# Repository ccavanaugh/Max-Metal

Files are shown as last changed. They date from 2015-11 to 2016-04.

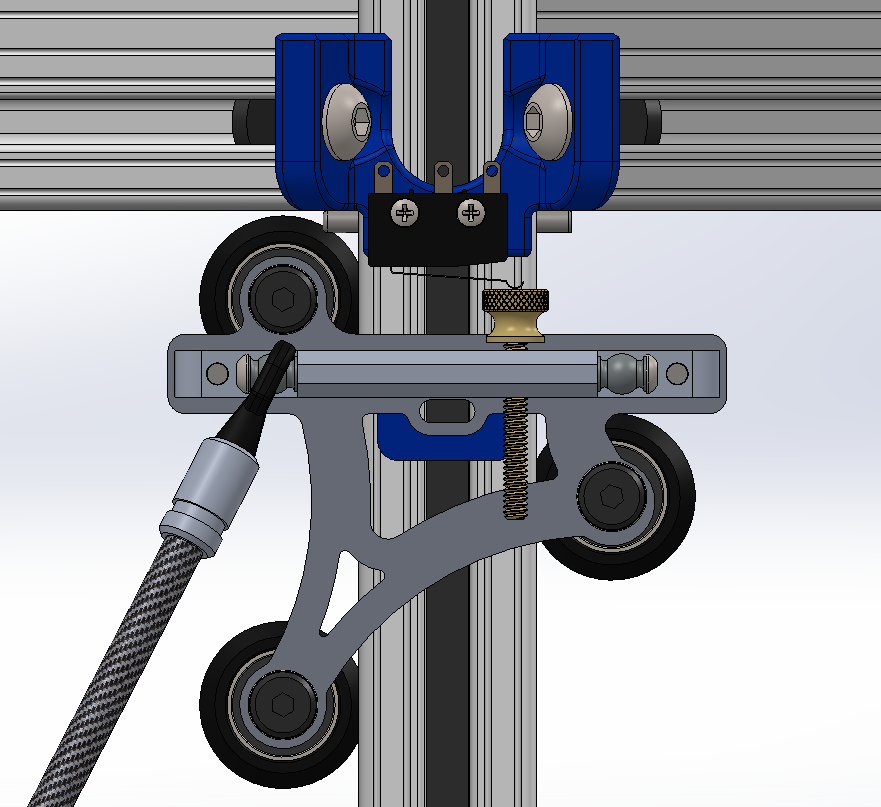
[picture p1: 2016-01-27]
Limit Switch Bracket v2.png

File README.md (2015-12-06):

# Max Metal Delta Printer Files

License
<br />This work is licensed under a <a rel="license" href="http://creativecommons.org/licenses/by-sa/4.0/">Creative Commons Attribution-ShareAlike 4.0 International License</a>.

These files are designed to be used with the all Aluminum Delta printer frame that can be purchased from [Trick Laser](http://www.tricklaser.com/)

## Print recommendations
All parts are deigned to be printed with a layer height of 0.1 mm.  Use of a slicer that can combine infill layers is highly recommended to reduce print time.  
I am printing 0.1 mm layers with 3 stacked layer (0.3 mm) for all sparse infill.  

Slic3r and Kisslicer Pro are known to be capable.  
 
## Small parts
The *Idler Hub* is an optional design vs. using the Open Builds idler assembly.  2 are required for each tower along 
with 2X 11 mm OD X 4 mm Wide x 5 mm ID bearings.  v2 of the part is ment for the thicker idler arms that are now provided
with all kits.

The *Trick Truck Belt Spacer* is required to keep the belt parallel to the axis of travel if you are using Trick Trucks.

These parts must be printed at 100% infill at 0.1 mm layer height. A larger layer height may create dimensional issues
  depending on the slicer used.  
  
  They must be flat!  PLA should provide sufficient strength.
  
## Tensioner Cap
Print at 80-100% infill.  The jack screws will put stress on the parts as will final tightening the of 5mm idler screw.
If you use these, you will need to replace the stock 30mm long idler screw with a 35mm long screw.  A pair of 3mm x 16mm long screws
and 3mm nyloc nuts will be need for tensioning.

## EZStruder Mount
This part is chunky.  We don't want it flexing under heavy retractions and it will see some radiated heat because of
proximity to the stepper motor.  Print with 20% infill.  

ABS or a nylon material is best, but PLA should be fine if your
stepper is not running hot or is actively cooled.

## Power Supply Bracket
Print with 25% or denser infill.  It should not see much heat so PLA is fine.

## Spool Cone
Print with support enabled

## End Stop Cap
Small caps for the end stop screws you can put a wrench on or turn by hand.  Stick the screw through with the head going into the counter-bore.
Fill flush with epoxy.

## Remaining parts
The other parts may be printed with infill and layer heights to suit.

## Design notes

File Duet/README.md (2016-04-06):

Two 0.50" Spacers are needed to support the Duet PCB at one end.  The LED/Connector end will slot and float into the side plate
Max length for the PCB mount screws is 30mm, otherwise it will hit the aluminum extrusion.  You do not want to ground out against the aluminum extrusion.

Use 6-32 X 1" Screws and nylocs to join the plates

Two 6-32 X 1 1/2" Screws and nylocs are used for the LCD housing

The FSR bracket uses 2 3mm x 12mm screws or you can use glue or PSA to attach it to the rear plate.  The FSR board should snap in place, but a small thru hole has been added for a self tapping screw if needed.

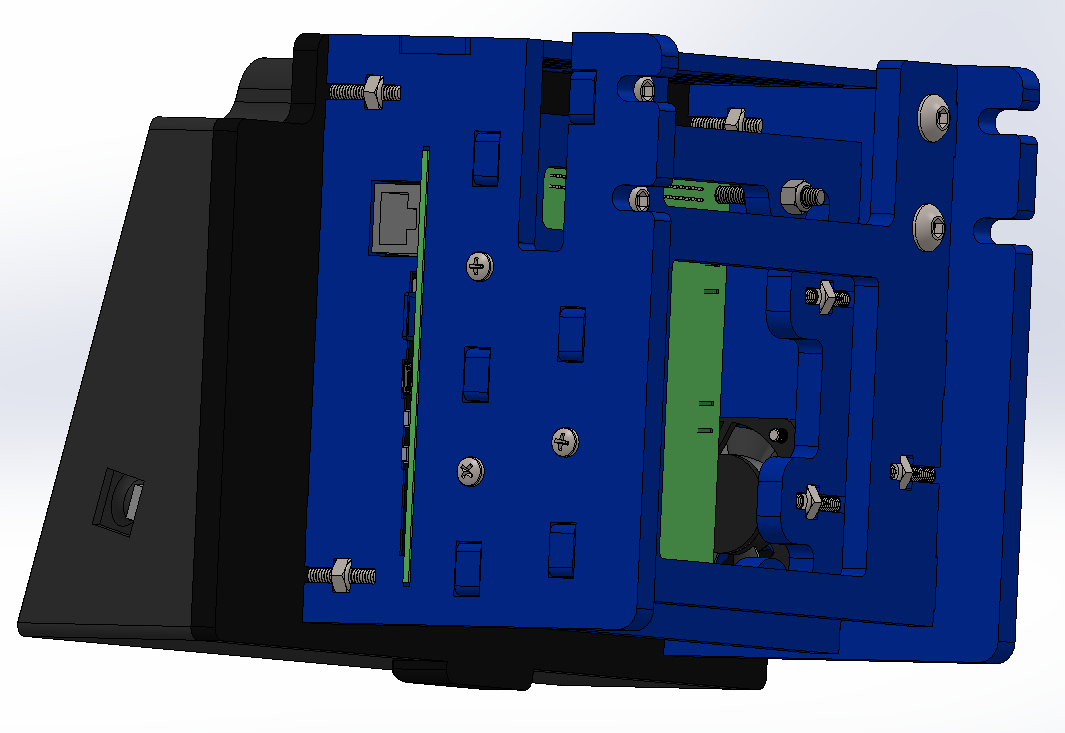
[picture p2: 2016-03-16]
Duet/Side.PNG

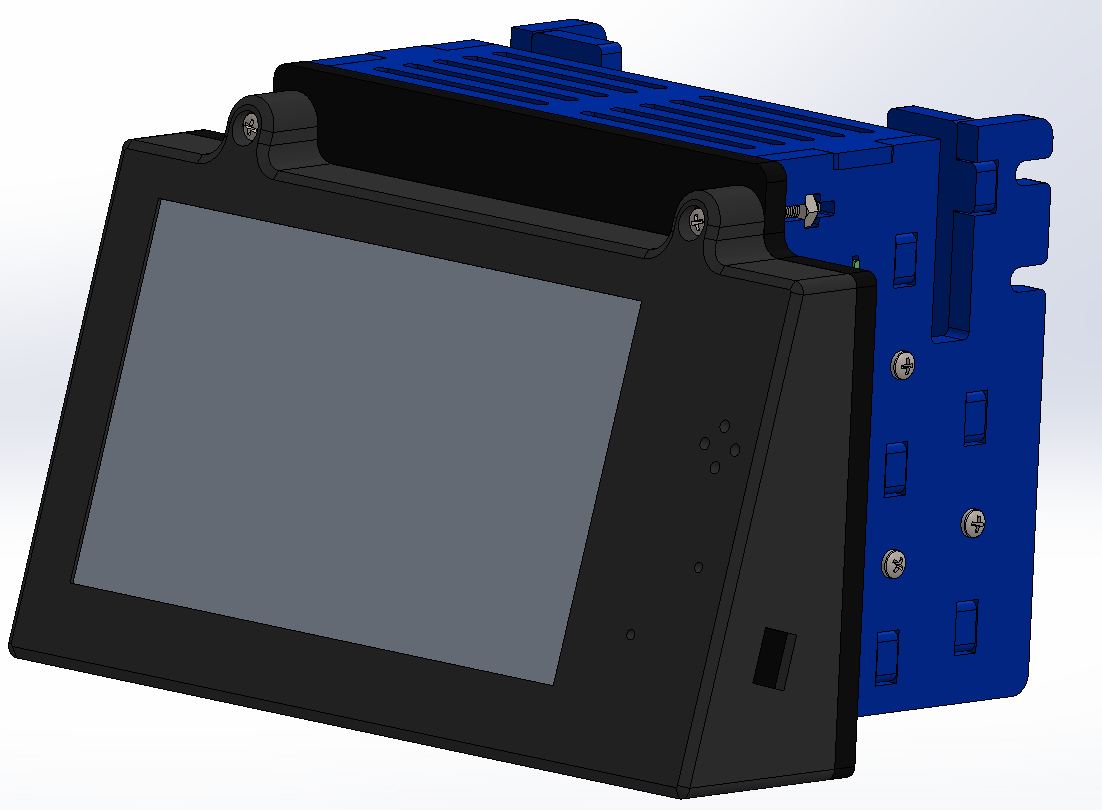
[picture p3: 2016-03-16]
Duet/Front.PNG

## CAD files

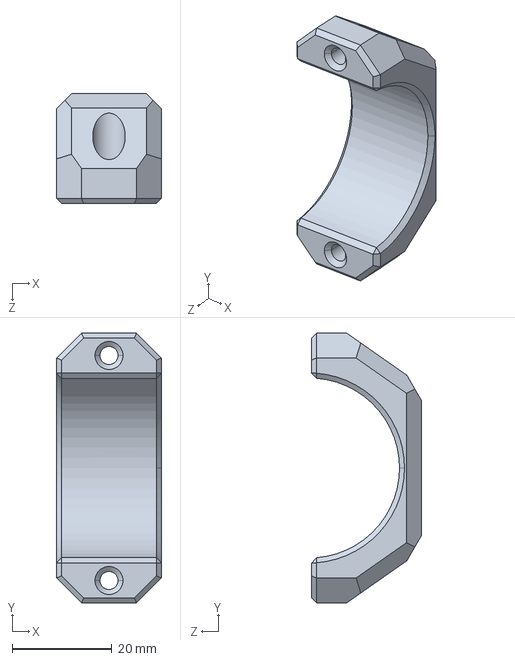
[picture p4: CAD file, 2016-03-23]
BondTech/BondTech Clamp.STEP
21.0 x 54.0 x 22.0 mm

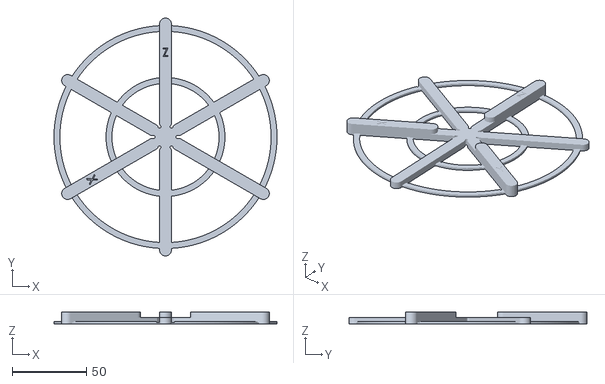
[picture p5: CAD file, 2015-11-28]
Calibration/60 DEGREE CALIBRATION OBJECT.STL
150.0 x 160.0 x 8.20

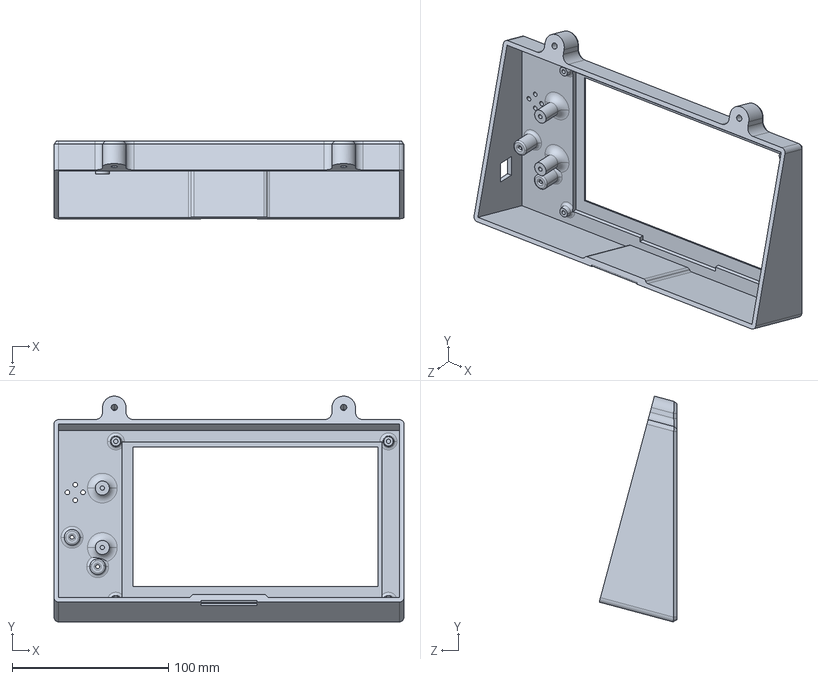
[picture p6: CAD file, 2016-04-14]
Duet/PanelDue 7-LCD Case.STEP
224.0 x 144.5 x 49.6 mm

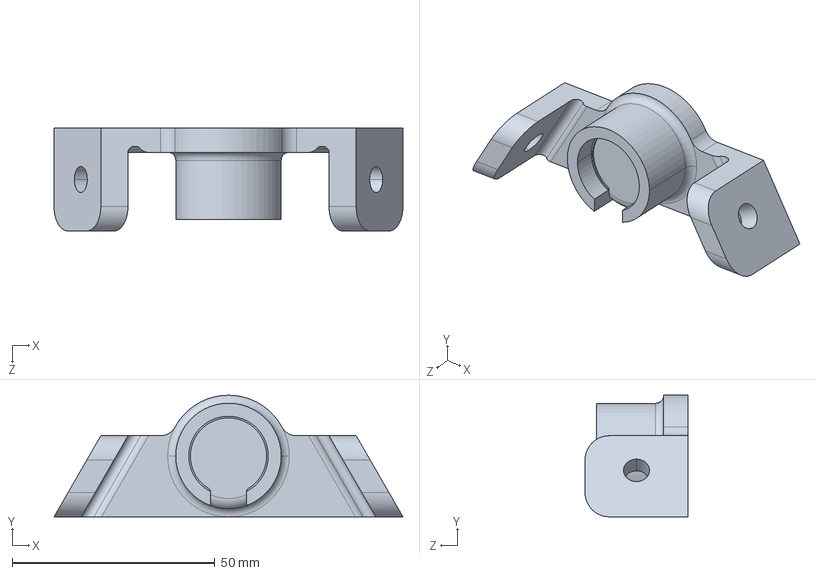
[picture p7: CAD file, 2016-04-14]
FSR BRACKET-Z.STEP
86.1 x 30.0 x 25.4 mm

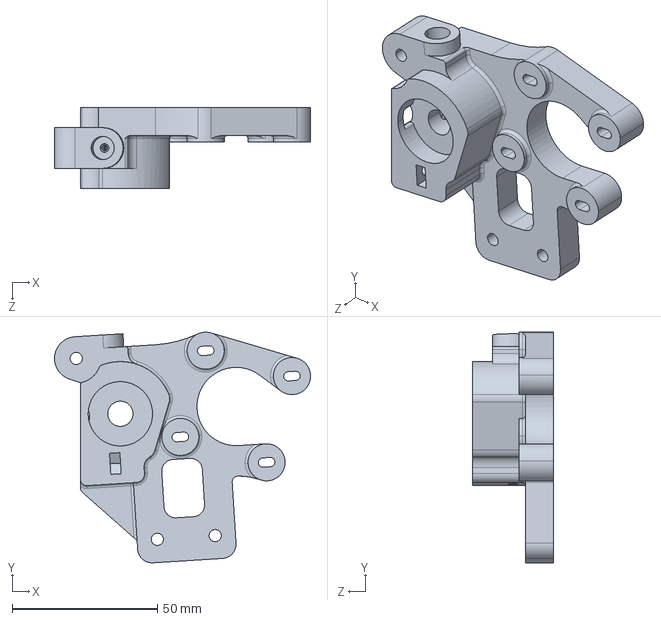
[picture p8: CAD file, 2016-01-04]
Geared Extuder/Extruder Frame - Delta.STEP
88.3 x 79.5 x 28.0 mm

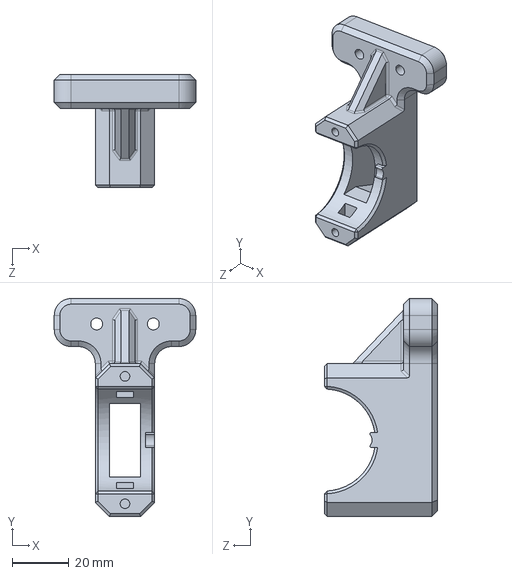
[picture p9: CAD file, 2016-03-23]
BondTech/BondTechBracket.STEP
50.0 x 77.0 x 40.0 mm

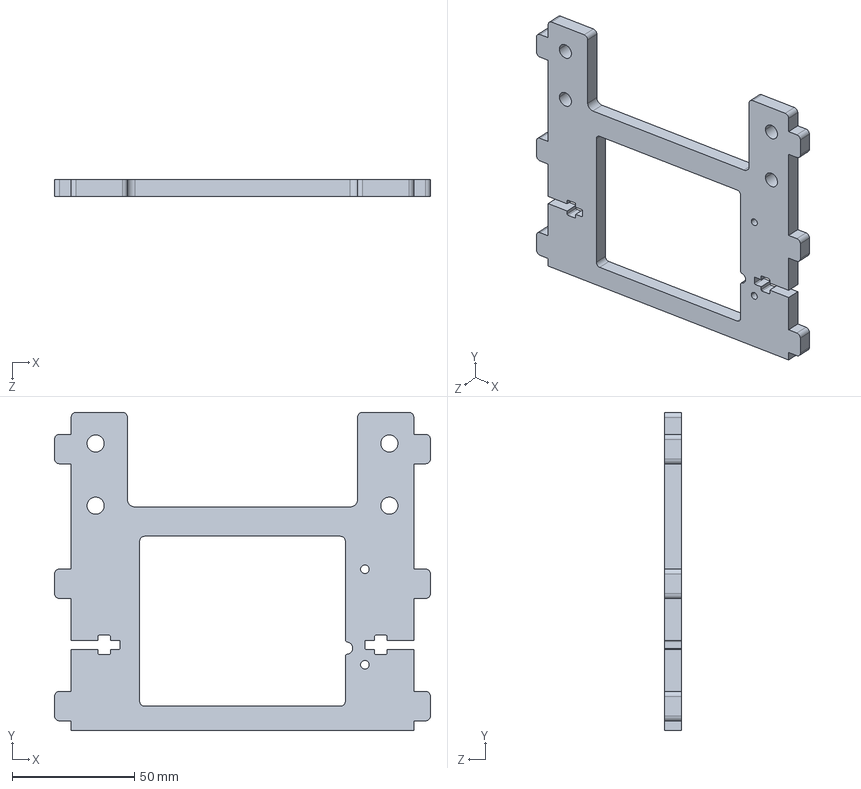
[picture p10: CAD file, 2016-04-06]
Duet/Duet Housing-Rear Plate.STEP
153.6 x 130.0 x 6.80 mm

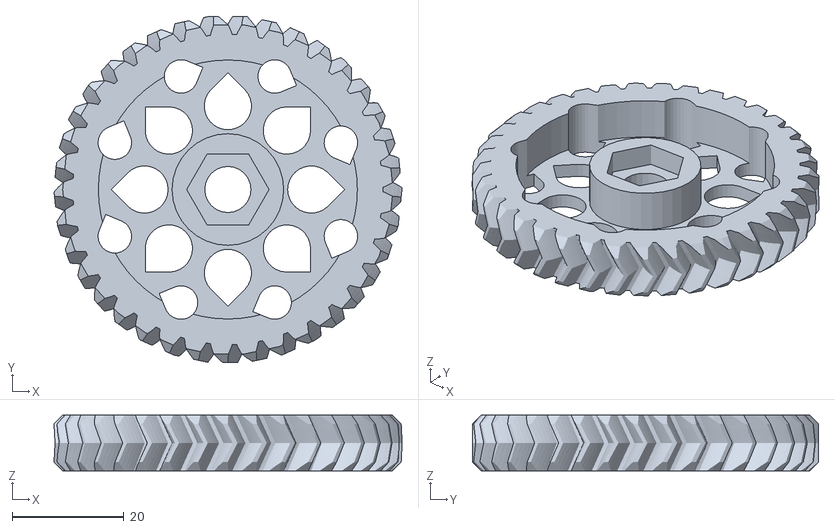
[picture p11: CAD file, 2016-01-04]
Geared Extuder/herringbone-gear-large.stl
62.3 x 62.1 x 10.0

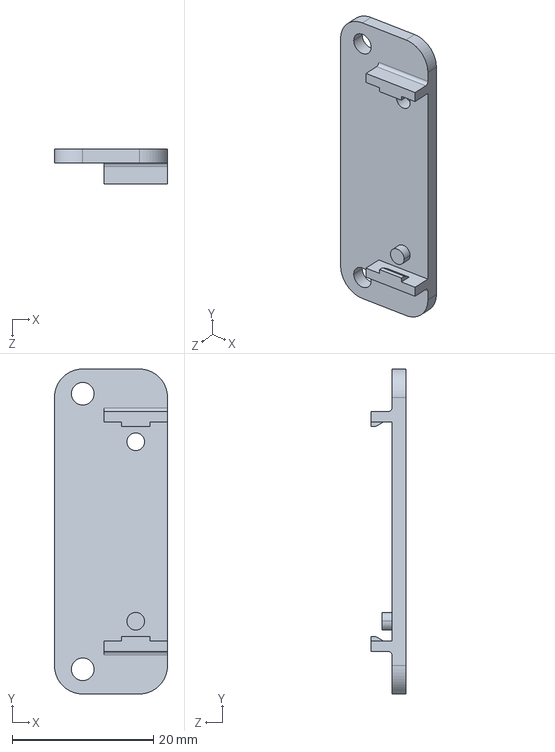
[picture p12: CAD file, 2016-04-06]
Duet/FSR Board Bracket.STEP
16.0 x 46.0 x 5.00 mm

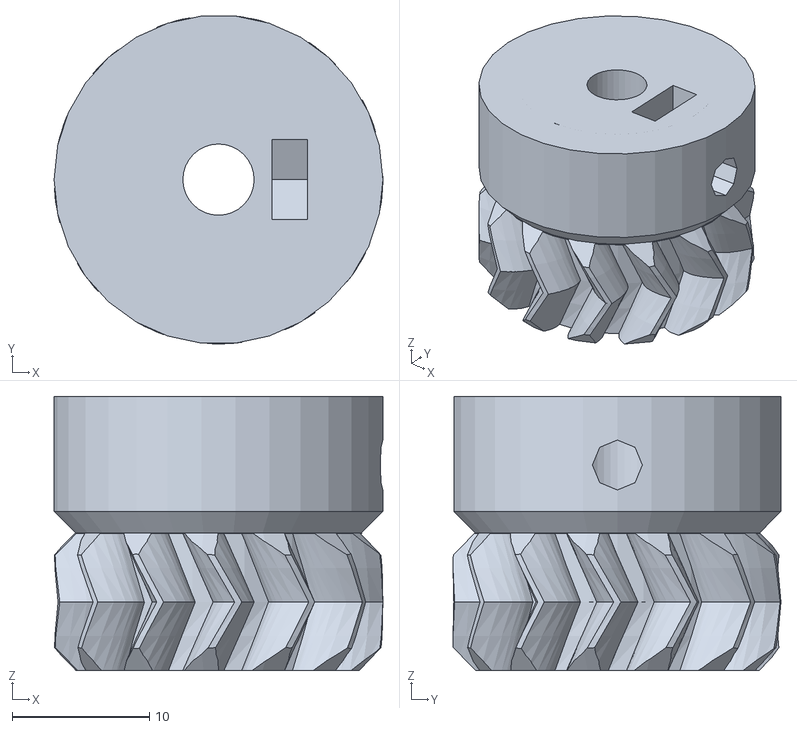
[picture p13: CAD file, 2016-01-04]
Geared Extuder/herringbone-gear-small.stl
24.0 x 23.9 x 20.0

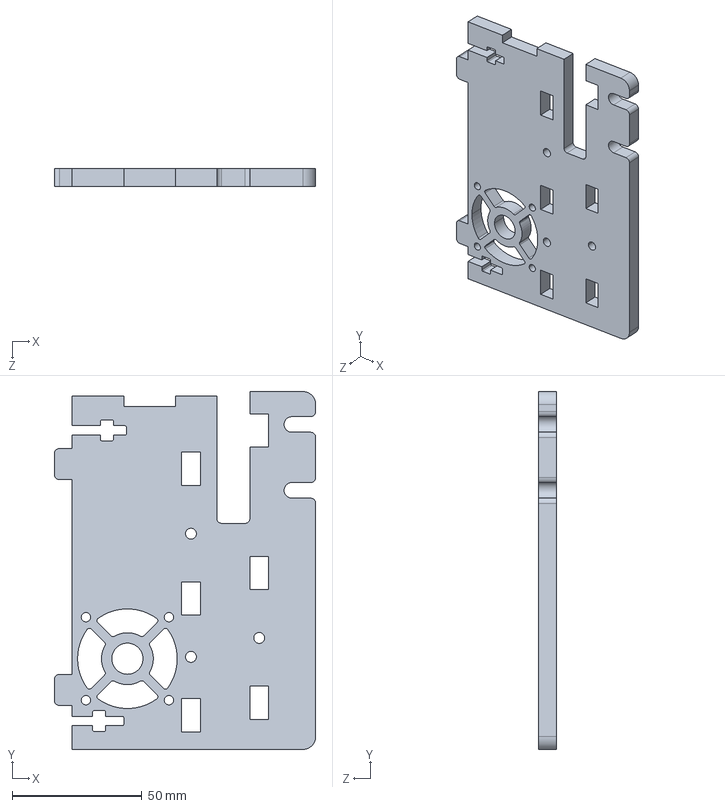
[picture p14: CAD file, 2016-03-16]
Duet/Duet Housing-Left Side Plate.STEP
100.8 x 138.0 x 6.80 mm

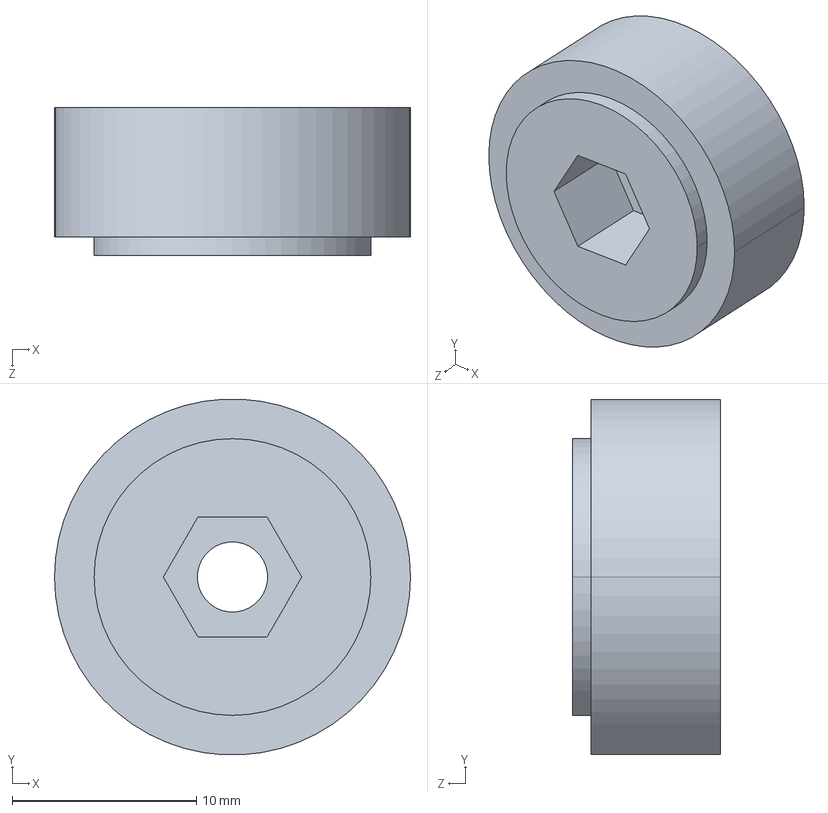
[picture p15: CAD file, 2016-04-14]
FSR Piston.STEP
19.3 x 19.3 x 8.00 mm

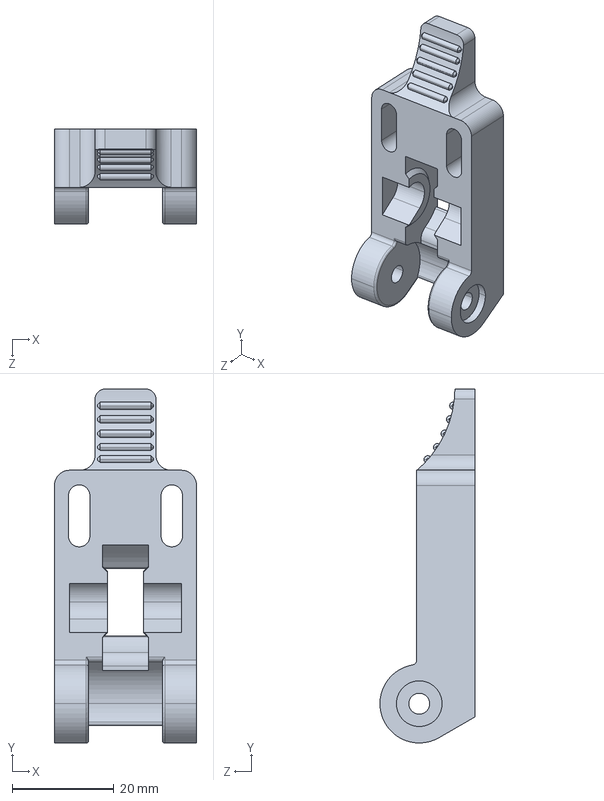
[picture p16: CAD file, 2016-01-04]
Geared Extuder/Guide.STEP
28.0 x 69.7 x 18.8 mm

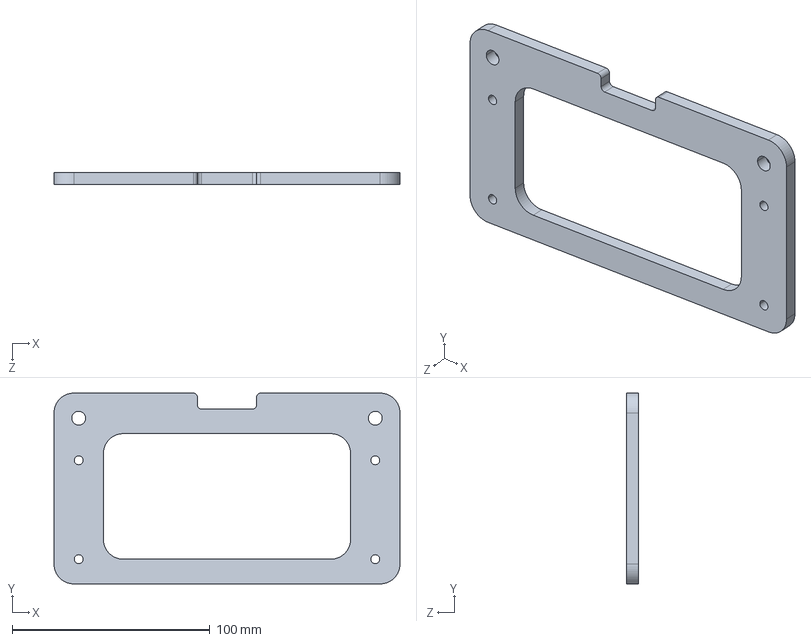
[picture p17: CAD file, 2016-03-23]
MW Power Supply Bracket.STEP
175.0 x 96.5 x 6.00 mm

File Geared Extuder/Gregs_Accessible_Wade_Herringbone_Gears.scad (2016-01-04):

// OpenSCAD Herringbone Wade's Gears Script
// (c) 2011, Christopher "ScribbleJ" Jansen
//
// Thanks to Greg Frost for his great "Involute Gears" script.
//
// Licensed under the BSD license.
include <MCAD/involute_gears.scad> 
include <MCAD/teardrop.scad> 

// $fa = 24;

// set to 0 for meshed gears, 1 for printing plate with gears flipped and laid flat
printing = 1;

// OPTIONS COMMON TO BOTH GEARS:
distance_between_axles = 40.00;
gear_h = 10;
gear_shaft_h = 10;


// GEAR1 (SMALLER GEAR, STEPPER GEAR) OPTIONS:
// It's helpful to choose prime numbers for the gear teeth.
gear1_teeth = 13;
gear1_shaft_d = 5.2;  			// diameter of motor shaft
gear1_shaft_r  = gear1_shaft_d/2;	
// gear1 shaft assumed to fill entire gear.
// gear1 attaches by means of a captive nut and bolt (or actual setscrew)
gear1_setscrew_offset = gear_h / 2;			// Distance from motor on motor shaft.
gear1_setscrew_d         = 3 / cos(180 / 8) + 0.4;
gear1_setscrew_r          = gear1_setscrew_d/2;
gear1_captive_nut_d = 5.5 / cos(180 / 6) + 0.4;
gear1_captive_nut_r  = gear1_captive_nut_d/2;
gear1_captive_nut_h = 2.6;


// GEAR2 (LARGER GEAR, DRIVE SHAFT GEAR) OPTIONS:
gear2_teeth = 37;
gear2_shaft_d = 8.2;
gear2_shaft_r  = gear2_shaft_d/2;
// gear2 has settable outer shaft diameter.
gear2_shaft_outer_d = 20;
gear2_shaft_outer_r  = gear2_shaft_outer_d/2;

// gear2 has a hex bolt set in it, is either a hobbed bolt or has the nifty hobbed gear from MBI on it.
gear2_bolt_hex_d       = 12.9;	//12.8
gear2_bolt_hex_r        = gear2_bolt_hex_d/2;
// gear2_bolt_sink: How far down the gear shaft the bolt head sits; measured as distance from outer face of gear.
gear2_bolt_sink          = 4;
// gear2's shaft is a bridge above the hex bolt shaft; this creates 1/3bridge_helper_h sized steps at top of shaft to help bridging.  (so bridge_helper_h/3 should be > layer height to have any effect)
bridge_helper_h= 0.35 * 3;

gear2_rim_margin = 0;
gear2_cut_circles  = 5;

// gear2 setscrew option; not likely needed.
gear2_setscrew_offset = 0;
gear2_setscrew_d         = 0;
gear2_setscrew_r          = gear2_setscrew_d/2;
// captive nut for the setscrew
gear2_captive_nut_d = 0;
gear2_captive_nut_r  = gear2_captive_nut_d/2;
gear2_captive_nut_h = 0;

// distance from center of M8 shaft to closest motor screw, so we can position access holes appropriately
motor_mount_access_radius = sqrt(((31 / 2) * (31 / 2)) * 2);


// Tolerances for geometry connections.
// AT=0.02;
AT=0.01;
ST=AT*2;
TT=AT/2;


module bridge_helper()
{
	difference()
	{
		translate([0,0,-bridge_helper_h/2])
		cylinder(r=gear2_bolt_hex_r+TT, h=bridge_helper_h+TT,$fn=6,center=true);
		translate([0,0,-bridge_helper_h/2])
		cube([gear2_bolt_hex_d+ST, gear2_shaft_d, bridge_helper_h+AT], center=true);
	}
}



module gearsbyteethanddistance(t1=13,t2=51, d=60, teethtwist=1, which=1)
{
	cp = 360*d/(t1+t2);

	g1twist = 360 * teethtwist / t1 / 2;
	g2twist = 360 * teethtwist / t2 / 2;

	g1p_d  =  t1 * cp / 180;
	g2p_d  =  t2 * cp / 180;
	g1p_r   = g1p_d/2;
	g2p_r   = g2p_d/2;

	echo(str("Your small ", t1, "-toothed gear will be ", g1p_d, "mm across (plus 1 gear tooth size) (PR=", g1p_r,")"));
	echo(str("Your large ", t2, "-toothed gear will be ", g2p_d, "mm across (plus 1 gear tooth size) (PR=", g2p_r,")"));
	echo(str("Your minimum drive bolt length (to end of gear) is: ", gear2_bolt_sink+bridge_helper_h, "mm and your max is: ", gear_h+gear_shaft_h, "mm."));
	echo(str("Your gear mount axles should be ", d,"mm (", g1p_r+g2p_r,"mm calculated) from each other."));
	if(which == 1)
	{
		// GEAR 1
		difference()
		{
			render()
			union()
			{
				translate([0,0,(gear_h/2) - TT])
					gear(	twist = g1twist, 
						number_of_teeth=t1, 
						circular_pitch=cp, 
						gear_thickness = gear_shaft_h + (gear_h/2)+TT,
						rim_thickness = (gear_h/2)+TT, 
						rim_width = 0,
						hub_thickness = (gear_h/2)+TT, 
						hub_width = 0,
						bore_diameter=0);
	
				translate([0,0,(gear_h/2) + TT]) rotate([180,0,0]) 
					gear(	twist = -g1twist, 
						number_of_teeth=t1, 
						circular_pitch=cp, 
						gear_thickness = (gear_h/2)+TT, 
						rim_thickness = (gear_h/2)+TT, 
						hub_thickness = (gear_h/2)+TT, 
						bore_diameter=0); 
				translate([0, 0, (gear_h * 1.5) - TT])
					cylinder(r=g1p_r + (cp / 180), h=gear_shaft_h, center=true);
			}
			//DIFFERENCE:
			//shafthole
			translate([0,0,-TT]) 
				cylinder(r=gear1_shaft_r, h=gear_h+gear_shaft_h+ST, $fn=32);

			//setscrew shaft
			translate([0,0,gear_h+gear_shaft_h-gear1_setscrew_offset])
				rotate([0,90,0])
				cylinder(r=gear1_setscrew_r, h=g1p_d + (cp / 180), $fn=8);

			//setscrew captive nut
			translate([(g1p_r)/2, 0, gear_h+gear_shaft_h-gear1_setscrew_offset]) 
				union() {
					translate([0, 0, gear1_captive_nut_r])
						cube([gear1_captive_nut_h, gear1_captive_nut_d * cos(30), gear1_setscrew_offset+ST],center=true);
					rotate([0, 90, 0])
						cylinder(h=gear1_captive_nut_h, r=gear1_captive_nut_r, center=true, $fn=6);
				}
			
		
		}
	}
	else
	{
		// GEAR 2
		difference()
		{
			render()
			union()
			{
				translate([0,0,(gear_h/2) - TT])
					gear(	twist = -g2twist, 
						number_of_teeth=t2, 
						circular_pitch=cp, 
						gear_thickness = (gear_h/2)+TT, 
						rim_thickness = (gear_h/2)+TT, 
						rim_width = gear2_rim_margin,
						hub_diameter = gear2_shaft_outer_d,
						hub_thickness = (gear_h/2)+TT, 
						bore_diameter=0); 
	
				translate([0,0,(gear_h/2) + TT]) rotate([180,0,0])
					gear(	twist = g2twist, 
						number_of_teeth=t2, 
						circular_pitch=cp, 
						gear_thickness = (gear_h/2)+TT, 
						rim_thickness = (gear_h/2)+TT, 
						rim_width = gear2_rim_margin,
						hub_diameter = gear2_shaft_outer_d,
						hub_thickness = (gear_h/2)+TT, 
						bore_diameter=0); 
			}
			//DIFFERENCE:
			//shafthole
			translate([0,0,-TT]) 
				cylinder(r=gear2_shaft_r / cos(180 / 24), h=gear_h+gear_shaft_h+ST, $fn=24);

			//setscrew shaft
			translate([0,0,gear_h+gear_shaft_h-gear2_setscrew_offset])
				rotate([0,90,0])
				cylinder(r=gear2_setscrew_r, h=gear2_shaft_outer_d);

			//setscrew captive nut
			translate([(gear2_shaft_outer_d)/2, 0, gear_h+gear_shaft_h-gear2_captive_nut_r-gear2_setscrew_offset]) 
				translate([0,0,(gear2_captive_nut_r+gear2_setscrew_offset)/2])
					#cube([gear2_captive_nut_h, gear2_captive_nut_d, gear2_captive_nut_r+gear2_setscrew_offset+ST],center=true);

			//trim shaft
			difference()
			{
				translate([0,0,gear_h+AT])	cylinder(h=gear_shaft_h+ST, r=g2p_r);
				translate([0,0,gear_h])	cylinder(h=gear_shaft_h, r=gear2_shaft_outer_r);
			}

			//hex bolt nut socket
			translate([0,0,-AT]) cylinder(r=gear2_bolt_hex_r  / cos(180 / 6), h=gear2_bolt_sink, $fn=6);

			// sunken face
			translate([0, 0, gear_h / 4])
				difference() {
					cylinder(r = g2p_r - (cp / 45), h=gear_h, center=true, $fn=64);
					cylinder(r = gear2_shaft_outer_r, h=gear_h + TT, center=true, $fn=32);
				}

			// motor mount access screw
			for(i = [0:7]) {
				rotate([0, 0, (45 * i) + 22.5])
					translate([motor_mount_access_radius, 0, gear_h / 2])
					rotate([0, 90, 90])
					teardrop(3, gear_h * 2, 90);						
			}

			// weight/plastic reduction and branding
			for (i = [0:7]) {
				rotate([0, 0, 45 * i])
				translate([gear2_shaft_outer_r + (g2p_r / 6) + AT, 0, gear_h / 2])
					rotate([0, 90, 0])
					teardrop(g2p_r / 7, gear_h * 2, 90);
			}
		}

		// hex bolt shaft bridge aid.
		/*
		translate([0, 0, gear2_bolt_sink]) {
			translate ([0,0,])
				bridge_helper();
			translate ([0,0,bridge_helper_h/3])
				rotate([0,0,60]) bridge_helper();
			translate ([0,0,((bridge_helper_h/3)*2)])
				rotate([0,0,-60]) bridge_helper();
		}
		/**/	
	}
	
}


t1 = gear1_teeth;
t2 = gear2_teeth;
cp = 360*distance_between_axles/(t1+t2);
g1p_d  =  t1 * cp / 180;
g2p_d  =  t2 * cp / 180;
g1p_r   = g1p_d/2;
g2p_r   = g2p_d/2;


translate([printing * cp / -35, 0, 0])
	//render()
		translate([-g1p_r,0,0]) rotate([0,0,($t*360/gear1_teeth)]) {
			intersection() {
				union() {
					translate([0, 0, 0]) cylinder(r1=g1p_r, r2=g1p_r + 5, h=5.1);
					translate([0, 0, 5]) cylinder(r2=g1p_r, r1=g1p_r + 5, h=5.1);
					translate([0, 0, 10]) cylinder(r1=g1p_r, r2=g1p_r + 10, h=10.1);
				}
				gearsbyteethanddistance(t1 = gear1_teeth, t2=gear2_teeth, d=distance_between_axles, which=1);
			}
		}


translate([0, 0, gear_h * printing]) rotate([180 * printing, 0, 0])
	//render()
		translate([g2p_r,0,0])  rotate([0,0,($t*360/gear2_teeth)*-1]) {
			intersection() {
				union() {
					translate([0, 0, 0]) cylinder(r1=g2p_r, r2=g2p_r + (cp / 180), h=(cp / 180));
					translate([0, 0, (cp / 180) - 0.01]) cylinder(r=g2p_r + (cp / 180), h=10.02 - (cp / 180) - (cp / 180));
					translate([0, 0, 10 - (cp / 180)]) cylinder(r2=g2p_r, r1=g2p_r + (cp / 180), h=(cp / 180));
					translate([0, 0, 10]) cylinder(r1=g2p_r, r2=g2p_r + (cp / 180) + 0.1, h=(cp / 180) + 0.2);
				}
				gearsbyteethanddistance(t1 = gear1_teeth, t2=gear2_teeth, d=distance_between_axles, which=2);
			}
		}
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

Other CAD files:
FSR BRACKET-X.STEP
FSR BRACKET-Y.STEP
Duet/Duet Housing-Right Side Plate.STEP
Duet/Duet Housing Front Cover - 7 LCD.STEP
BondTech/BondTech Clamp.STL
BondTech/BondTechBracket.STL
Drill Guide.STL
Duet/Duet Housing Front Cover - 7 LCD.STL
Duet/Duet Housing-Left Side Plate.STL
Duet/Duet Housing-PCB Plate.STEP
Duet/Duet Housing-PCB Plate.STL
Duet/Duet Housing-Rear Plate.STL
Duet/Duet Housing-Right Side Plate.STL
Duet/Duet Housing-Top Plate.STL
Duet/FSR Board Bracket.STL
Duet/PanelDue 7-LCD Case.STL
EZStruder Mount.STL
Electronics Housing Bracket.STEP
Electronics Housing Bracket.STL
Electronics Housing Side Bracket - Smoothie Left.STEP
Electronics Housing Side Bracket - Smoothie Left.STL
Electronics Housing Side Bracket - Smoothie Right.STEP
Electronics Housing Side Bracket - Smoothie Right.STL
Electronics Housing Side Bracket.STEP
Electronics Housing Side Bracket.STL
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

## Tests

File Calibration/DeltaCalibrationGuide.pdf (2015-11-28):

# Calibrating for Angularity Error and Improved Bed Flatness

After ultimately rebuilding my delta printer with a MAX METAL frame and Trick Trucks purchased from Trick Laser, I had significantly reduced printed part dimensional error but was left with a nagging angularity error that was more evident on larger parts. I spent a fair amount of time qualifying the frame and was able to confirm the towers were square within 0.1° and equilateral within 0.0025”. The arms were verified to be equal in length which left the effector and the ujoint carriage as the next possible sources of error. When I originally built the machine I had to file and fit the ujoints. I suspect that despite my “careful” approach, I ultimately introduce some inaccuracies during the ujoint fitting process..

My search for an easy to implement firmware solution and calibration for the next step of improved part accuracy led me to a means of simple mechanical adjustment.

## Error Mapping / Calibration

If you have witnessed the processes used to error map a CNC or CMM using a known ball bar or laser measurement system, they ultimately depend on having some sort of calibrated standard to measure against.

The current state of automatic bed leveling and calibration processes can dramatically improve visual printed print quality, but there is no guarantee of accurate part angles and sizes. They use the bed as a 2D planar reference which is not sufficient to compensate for 3D dimensional errors in the machine.

My goal is to reduce as much of the mechanical error in the machine as possible and then let the automatic calibration tools perform the fine tuning to help with first layer adhesion and part appearance.

These Instructions are based on a method presented by Taede de Jong (http://www.thingiverse.com/thing:745523). I recommend taking the time to read the process he describes which makes it easy to understand a manual approach of error compensating for machine build inaccuracies. He details how to make firmware modifications to fine tune the calibration. Repetier and Smoothie currently allow for error mapping some of these parameters within the configuration without modifying the code.

I will be focusing primarily on addressing the observed angularity error without use of firmware changes by minimizing physical geometry error within the printer.

## Process

The process of checking and adjusting is iterative. I recommend focussing on one tower at a time to avoid too many changes which can make validation of improvement difficult. My experience was it took 4 total print cycles.

1 of 7 | Craig Cavanaugh 2015-11-28

- 1st was a base line print
- 2nd was to adjust the X tower
- 3rd was to validate a 2nd adjustment to the X tower (this was then used for the Y tower)
- 4th was to validate an adjustment to the Y tower.

If you have a means of directly measuring the angularity error of the calibration object and doing a bit of trig work, it’s possible to minimize the iterations.

Print time is approximately 1 hour for the calibration piece and about 7.8m of ∅1.73mm filament.

### Tools

- A good quality 30/60 drafting triangle. I prefer a transparent triangle as it makes checking with a light source easier for me. If you want to check for tower parallelism, get two triangles. The 2nd drafting triangle can be a 45.

### Assumptions

- The printer towers are square and equidistance within reasonable use of hand tools. See the later part of this guide for a suggested technique.
- Arm lengths should be as equidistant as possible.
- The printer is calibrated well in regards to delta arm length, horizontal radius, end stop, etc.
- You are not printing with any other type of error correction in play to skew the results.
- The heated bed has had plenty of time to stabilize prior to printing to minimize dimensional errors after cooling.

### Calibration Part Print Instructions

- Use an easy to print material with minimal warping such as PLA.
- Avoid overfilling the part. If the top layers are not flat, it can make inspection more difficult.
- Print at 0.1 or 0.2mm layer height. (I used 0.2mm for the first layer and 0.1mm for the other layers). The calibration guide was designed with 0.2mm layers heights.
- Print exterior perimeters first for best accuracy.
- 1st layer smash will not impact the accuracy of the process.
- The printer needs to be tuned well enough to minimize blobs on perimeter surfaces. The calibration object is designed to tolerate blobs and errors on interior corners.
- I used 30% infill. Print to suit, but I would avoid use 100% infill.

## Iteration Process

- Print the calibration object and cleanup any blobs and strings as needed.
- Verify angles with the 60° triangle. After inspection of all angles, make a determination as to which tower will be left as a fixed reference. Jong’s approach uses the Z tower as the fixed reference. But close examination may identify one tower as being preferred.
- Shift the arms within the ujoint carriage as need.

- Example: If the angle between the X and Z tower is too large, then you need to shift the arms to create a clockwise rotation effectively reducing the physical angle between the towers.
- Iterate as needed.
- Focus on fixing angularity error before you consider length and width measurement errors.
- If you end up making a significant enough adjustment in angularity, it is possible you may need to reset the tower endstops between iterations. Tower zero heights do affect each other.

The Calibration Object that I have supplied has the following features.
- It can be checked with a quality drafting triangle. I don’t trust printed paper unless it’s a calibrated mylar print. (Old school optical comparator overlay for the “experienced”)
- Inside corners are relieved to prevent influence of blobs and corner radii that are a resultant of nozzle diameter and less than perfect print calibration.
- The part is tall enough that the top layer is higher than a typical drafting triangle to avoid risk of influence.
- The 3rd significant step in the part (with Tower indicators), gives you easy to measure geometry for size accuracy checks. (60mm x 8mm)
- The extra height lets you focus on angularity first before having to deal with bed level. Bed level should naturally improve as angularity improves.

## Sample Images

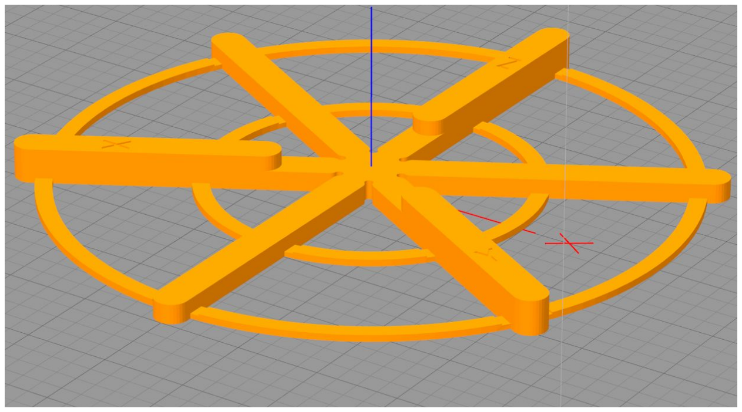
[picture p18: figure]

Calibration Object

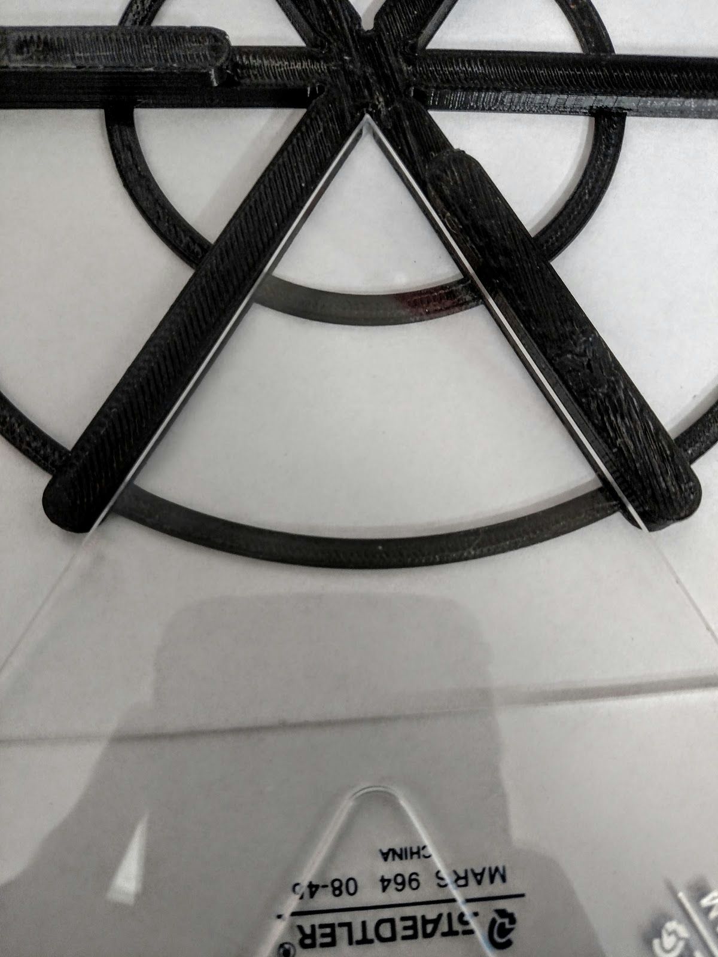
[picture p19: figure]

Sample check of the 60° angle.

## U-Joint Carriage Adjustment

Use of the Trick Laser Arms made adjustment easier, but it is possible without by placing shim washers on the axle between the ujoint and arm. I made adjustment room possible, by filling a bit of plastic off one side to allow a lateral shift. No matter the approach used, you want to ensure spacing between all arms are equidistance at all times. If using the stock aluminum or plastic ujoints, you can start with paper as a shim as a test and eventually replace with a more durable solution (McMaster sell sheets of PTFE shim stock).

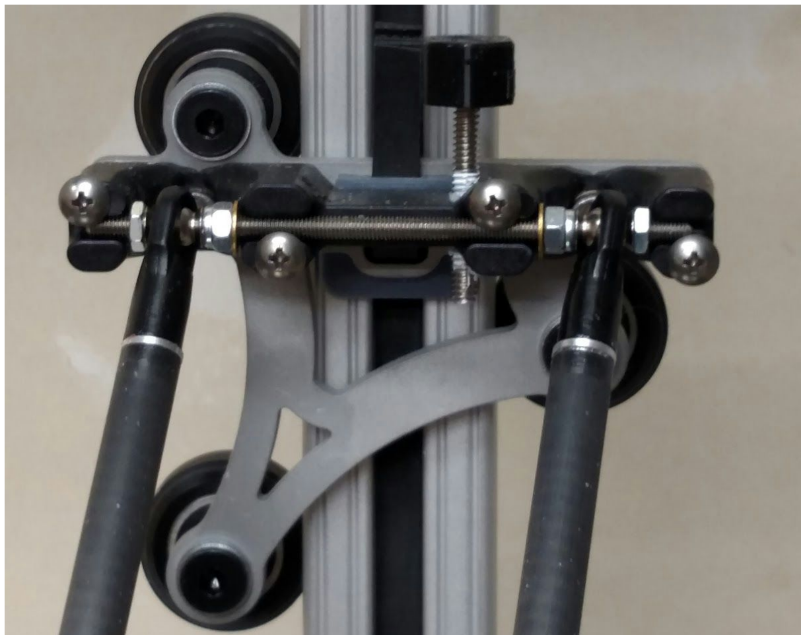
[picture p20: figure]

In this photo, you can see a gap in between the brass washer on the ujoint carriage and nut on the right while the washer and nut are tight on the left side. When I checked the X tower relative to the Z, I had an result angle that was about 61°. I removed a small amount of material off the left side of the ucarriage to allow room to shift it to the right. This small shift corrected the angularity error.

### Note:

Theoretically, it is possible to apply compensation to the effector instead of the ujoint carriage. I chose the ujoint carriage because I originally removed the most material from them when building the printer and assumed that this is where I introduced the most error.

## Checking for Square and Tower Parallelism

Below is the method I use to check the machine for square and tower parallelism. I’m not fond of using framing squares. They tend to be stamped and inaccurate unless you’ve tweaked it or spent the money for a good one, and they can break glass if dropped.

I always perform a final check against the bed with the glass plate installed. It’s alway a very good to check for square without the bed during the build of the machine to check frame geometry, but the bed needs to be square also.

When you tuck the triangle into the slot and rotate it at an angle, it removes all the play and forces it to square up on the extrusion nicely. This creates a repeatable process that avoids having to deal with the slight angle that exists on the exterior faces of the extrusion.

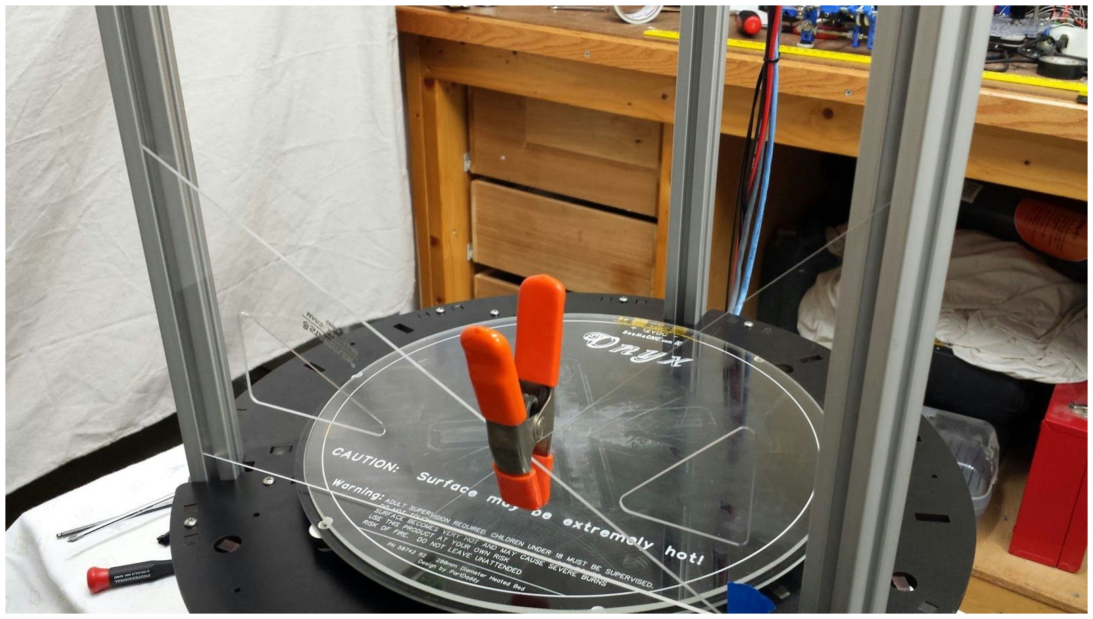
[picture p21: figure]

The spring clamp was used for photography purposes only.

If you squeeze the triangle against the extrusion (grip between the interior cutout of the triangle and the outside face of the extrusion and slide it to down the glass plate, you can easily check for square. Use of two triangle on opposite towers can show that both are square and parallel to each other. If one triangle is square to the bed and the other is not, you’ve got some assembly errors to sort out.

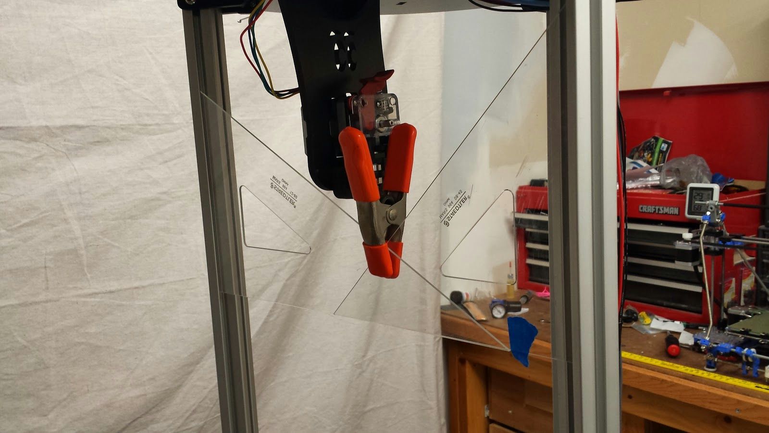
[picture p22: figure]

If you slide the triangles up to the top, mark the tip where one triangle overlaps the next and check for the same distance (mark) at the heated bed, you can easily identify parallelism error that is not evident at one height. The triangles should also be parallel to each other at their bases.

Next step is to check the distance and parallelism between the other remaining towers to verify they are all equidistant from one another.

If you prefer, a thin point permanent marker can be used to mark a triangle intersection and then use some rubbing alcohol to clean it off later. A buddy can be very helpful at this point.

This method is very repeatable and creates a precise visual method without use of expensive tools. You don’t need indicators, calipers, CMM’s, etc to ensure you have a good foundation to print dimensionally accurate parts.

When building my Rostock Max v1 printer, I tucked all towers tight radially in the slots, and then bumped two of the towers out radially to match the tower with the largest radial distance from center after first checking for equidistance. I did this with just the base assembly only, and after set, installed the top plate ensuring it did not bias the assembly by sanding on a slot or two. It’s takes a bit of patience, but it is doable.

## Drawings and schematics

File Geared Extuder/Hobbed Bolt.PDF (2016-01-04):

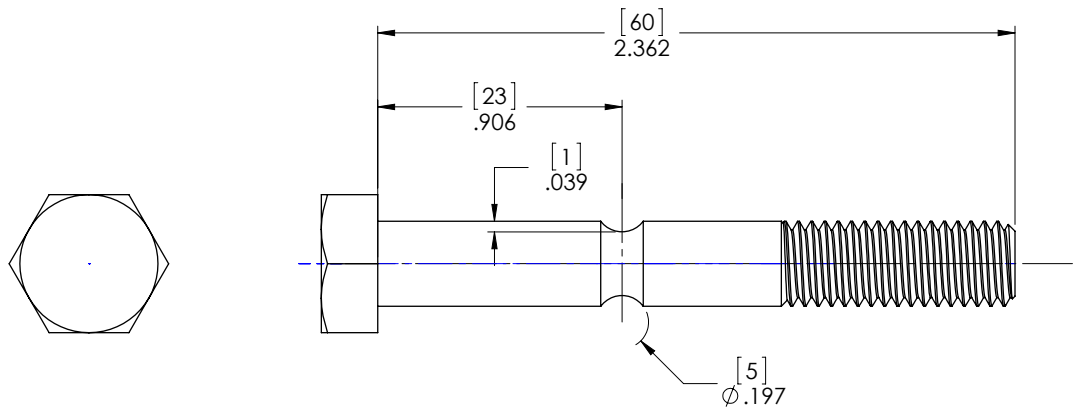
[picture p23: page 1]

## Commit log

2015-03-29 Initial release of the printable files
    [EZStruder Mount.STL, Heated Bed Insulator Bracket.STL, Idler Hub.STL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]
2015-03-29 Fixed orientation of the file
    [Power Supply Bracket.STL]
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2015-03-30 Updates
    Spool holder revisions. Sized the holes better and added a round wrap
    for better behavior
    [Spool Holder Bracket.STL, Spool Holder.STL]
2015-03-30 Add radius
    Improve part strength
    [Spool Arm.STL]
2015-04-01 Gen 2 spool holder
    Alternate spool holder design
    [Spool Cone.STL, Spool Holder Bracket 2.STL]
2015-04-04 Add drill guide for end stop wires
    [Drill Guide.STL]
2015-04-05 Fix height
    Correct height based on actual frame measurements
    [Idler Hub.STL]
2015-04-05 Fix hole location
    Correct radial hole location based on actual frame measurements
    [Heated Bed Insulator Bracket.STL]
2015-04-05 Add optional spacer for clearance
    Create some clearance to vent the power supply
    [Foot Riser.STL]
2015-04-05 Adjust spacing
    Shorten up, belt too close and not parallel
    [Trick Truck Belt Spacer.STL]
2015-04-07 Improved printability of the part
    [Heated Bed Insulator Bracket.STL]
2015-04-07 Add riser for the foot for better power supply ventilation
    [Foot Riser.STL]
2015-04-07 Improved printable design
    [Heated Bed Insulator Bracket.STL]
2015-04-07 Increased height by .12"
    1 3/4" screw is getting close to steeper motor screw. Reduce risk of
    damaging the screw.
    [Foot Riser.STL]
2015-04-07 Improve access to screw
    Improve access to all screws so the heated bed does not need to be
    pulled to remove the power supply
    [Power Supply Bracket.STL]
2015-04-11 Revised design
    Improve strength
    [Spool Holder Bracket 2.STL]
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2015-04-14 Reduce mass, use two bearings per cone
    [Spool Cone.STL]
2015-04-14 Improve wire routing
    add slot so wire can go over the top
    [Top Vertex.STL]
2015-04-14 Fix spacing, alignment, add wire routing
    [Electronics Housing Side Bracket.STL, Electronics Housing Top.STL, ReprapDiscount Plate.STL]
2015-04-25 Add features to key to extrusion
    Prevent twisting of the foot
    [Foot Riser.STEP, Foot Riser.STL]
2015-04-25 Export STEP
    Make STEP file available
    [Top Vertex.STEP]
2015-04-25 Remove pocket
    Pocket for screw is not needed
    [Power Supply Bracket.STEP, Power Supply Bracket.STL]
2015-04-25 Increase thru hole sizes
    Make assembly easier
    [Swith Bracket.STEP, Swith Bracket.STL]
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2015-04-25 Printable end stop clamp
    Stuff the 6-32 screw thru the cap and fill flush with expoxy
    [End Stop Cap.STEP, End Stop Cap.STL]
2015-04-25 Final version
    Working version of the optional idler hub
    [Idler Hub.STEP, Idler Hub.STL]
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2015-04-25 Assembly fix
    Omit one key for correctly assembly
    [Foot Riser.STEP, Foot Riser.STL]
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2015-05-09 Smoothie Board Specific side brackets
    Create Smoothie Board Specific side brackets for improved ease of use
    [Electronics Housing Side Bracket - Smoothie Left.STEP, Electronics Housing Side Bracket - Smoothie Left.STL, Electronics Housing Side Bracket - Smoothie Right.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]
2015-06-24 Add plate and reset button for Reprap GLCD
    Add plate and reset button for Reprap GLCD
    [GLCD Plate.STL, Reset Button.STL]
2015-06-26 Clearance LCD
    Clearance LCD
    [GLCD Plate.STL]
2015-08-02 Add missing STEP file
    Add missing STEP file
    [GLCD Plate.STEP]
2015-11-28 Add Calibration Part and Guide
    Add Calibration Part and Guide
    [60 DEGREE CALIBRATION OBJECT.STL]
2015-12-05 Version 2
    The idler arm design was changed soon after the first release of kits.
    v2 is for the newer revision. The revised idler arms have a continuous
    thickness while the first revision have a small step for the pulley.
    [Idler Hub v2.STEP, Idler Hub v2.STL]
2015-12-06 Add version 2 for the belt clamp
    Add a rib to bite into the belt to prevent slippage
    [Trick Truck Belt Clamp v2.STEP, Trick Truck Belt Clamp v2.STL]
2015-12-06 Tensioner Cap
    Belt Tensioner
    [Tensioner Cap.STEP, Tensioner Cap.STL]
2016-01-04 Geared extruder files
    Geared extruder files
    [Extruder Frame - Delta.STEP, Gregs_Accessible_Wade_Herringbone_Gears.scad, Guide.STEP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]
2016-01-27 Updated limit switch bracket
    Updated limit switch bracket. Uses less material. This replaces the
    "Top Vertex" component
    [Limit Switch Bracket.STEP, Limit Switch Bracket.STL]
2016-02-27 Version 3 of the Heated Bed Insulator Bracket
    Allows use of an unmodified SeeMeCNC bed insulator
    [Heated.Bed.Insulator.Bracket.v3.STEP, Heated.Bed.Insulator.Bracket.v3.STL]
2016-02-27 FSR specific bracket for heated bed
    Added a FSR specific heated bed bracket design and associated piston. This is designed for the SeeMeCNC heated bed and insulator.
    [FSR.BRACKET.STEP, FSR.BRACKET.STL, FSR.Piston.STEP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]
2016-03-12 Add Trick Truck STEP file
    Add Trick Truck STEP file
    [Trick Truck.STEP]
2016-03-12 Add FSR Bracket and Piston
    FSR specific piston and bracket components.
    [FSR BRACKET.STEP, FSR BRACKET.STL, FSR Piston.STEP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]
2016-03-16 Add Preliminary files for Duet housing
    [Duet Housing-Left Side Plate.STL, Duet Housing-PCB Plate.STL, Duet Housing-Rear Plate.STL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]
2016-03-16 Untested parts
    Untested parts
    [Duet Housing Front Cover - 7 LCD.STL, PanelDue 7-LCD Case.STL]
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2016-03-23 Improved FSR Bracket Design
    1 Each of the X, Y, and Z bracket are required. 3X of the piston are
    required
    [FSR BRACKET-X.STEP, FSR BRACKET-X.STL, FSR BRACKET-Y.STEP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]
2016-03-23 Add Mean Well power supply bracket
    Mean Well compatible power supply bracket
    [MW Power Supply Bracket.STEP, MW Power Supply Bracket.STL]
2016-03-23 Add Bondtech extruder clamp
    [BondTech Clamp.STEP, BondTech Clamp.STL, BondTechBracket.STEP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]
2016-04-06 Add bracket for JohnSL FSR board (version 1.2)
    [FSR Board Bracket.STEP, FSR Board Bracket.STL]
2016-04-06 Added mounting holes for the FSR bracket
    [Duet Housing-Rear Plate.STEP, Duet Housing-Rear Plate.STL]
2016-04-06 Add clearance of thru hole on the FSR bracket
    [Duet Housing-Rear Plate.STEP, Duet Housing-Rear Plate.STL]
2016-04-11 Reduce need for support
    chamfer on face exceeded 45
    [PanelDue 7-LCD Case.STEP]
2016-04-14 Update FSR Brackets
    Increase diameter to allow use of commonly available 3/4" OD rubber
    washers as pads/spacers on top of the FSR to distribute force.
    [FSR BRACKET-X.STEP, FSR BRACKET-X.STL, FSR BRACKET-Y.STEP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]
2016-04-14 Improve appearance, reduce material
    Improved border spacing around the LCD for improved appearance. Removed
    some excess material
    [PanelDue 7-LCD Case.STEP]
